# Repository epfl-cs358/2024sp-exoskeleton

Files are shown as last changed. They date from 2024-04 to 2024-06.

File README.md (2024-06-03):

# 2024sp-exoskeleton

<!-- PROJECT SHIELDS -->
<!--
-->
[][contributors-url]
[][license-url]

### Authors
- [Ewa Miazga](https://github.com/ewaMiazga)
- [Gabin Forestier](https://github.com/ForestDope)
- [Wei-En Hsieh](https://github.com/annhit29)
- [William Robert](https://github.com/AgeX21)
- [Benoit Morawiec](https://github.com/markh0rr)
- [Haris Malik](https://github.com/harismalik-1)

<!-- MARKDOWN LINKS & IMAGES -->
<!-- https://www.markdownguide.org/basic-syntax/#reference-style-links -->
<!-- change the contributors page -->

<!-- TABLE OF CONTENTS -->
<details>
  <summary>Table of Contents</summary>
  <ol>
    <li>
      <a href="#about-the-project">About The Project</a>
      <ul>
        <li><a href="#built-with">Built With</a></li>
        <li><a href="#motivation">Motivation</a></li>
        <li><a href="#goal">Goal</a></li>
        <li><a href="#final-result">Final Result</a></li>
      </ul>
    </li>
    <li>
      <a href="#getting-started">Getting Started</a>
      <ul>
        <li><a href="#prerequisites">Prerequisites</a></li>
      </ul>
    </li>
    <li>
      <a href="#building-the-exoskeleton">Building the Exoskeleton</a>
      <ul>
        <li><a href="#mechanical-parts">Mechanical Parts</a></li>
        <li><a href="#assembly">Assembly</a></li>
        <li><a href="#electronics">Electronics</a></li>
      </ul>
    </li>
    <li><a href="#software">Software</a></li>
    <li><a href="#problems">Problems</a></li>
    <li><a href="#possible-improvements--extensions">Possible Improvements & Extensions</a></li>
    <li><a href="#license">License</a></li>
  </ol>
</details>

<!-- ABOUT THE PROJECT -->
## About The Project

<!-- MOTIVATION -->
### Motivation

Nowadays, hand exoskeletons are commonly used for rehabilitation therapy following health accidents such as strokes. Its efficacy in muscle memory training has the potential to be exploited in the fields of music, technology, and rehabilitation therapy.

Our project aims to facilitate muscle memory training of various piano techniques for pianists seeking to strengthen specific muscles and refine pianistic skills with greater efficiency. By using a lightweight hand exoskeleton, we can enforce specific positions at a given rhythm that allows the user to acquire a specific technique more quickly compared to traditional training.

We want the user to be able to input a technique and a specific tempo that they wish to train using an accompanying software tied to the exoskeleton. This then allows the exoskeleton to reproduce the movements of the technique.

<p align="right">(<a href="#readme-top">back to top</a>)</p>

<!-- FINAL RESULT -->
### Final Result
At the end of the semester, we have an exoskeleton of a hand that functions as follows:

<p align="center">
    Demo GIF
</p>

See the demo of our project here: [Demo](./photos/demo.mp4)

Some photos for reference:

<p align="center">
     
     
</p>

It is controlled via a web application, which includes a feature for playing songs with preloaded files. Additionally, the device can record played pieces, aiding the learning process by allowing users to repeat the segments they prefer.
Each finger is operated by a separate motor, enabling simultaneous movement of all fingers. This design grants the device flexibility, allowing it to play almost any song desired.

<p align="right">(<a href="#readme-top">back to top</a>)</p>

<!-- GETTING STARTED -->
## Getting Started

<p align="right">(<a href="#readme-top">back to top</a>)</p>

<!-- BUILT WITH -->
### Built With 
* [][React-url]
* [][Python-url]
* [][Cpp-url]
* [][Flask-url]

<p align="right">(<a href="#readme-top">back to top</a>)</p>

<!-- PREREQUISITES -->
### Prerequisites

Comprehensive list of elements we used in our project along with needed equipment. To construct the device, one should
- buy:
  -	Arduino Uno Board
  -	Proto Shield ARDUINO V.R3
  -	Power supply GST60A12-P1J
  -	Board LM2596
  -	DC Power Jack PJ-102B
  -	4 Bowden cables
  -	4 Servo motors DMS15-270
  -	MIDI keyboard
  -	Velcro tape
  -	Sewing kit
  -	Threads
  -	Screws
  -	Small elastic bands

- have access to:
  -	3D printer with TPU filament
  -	3D printer with PET filament
  -	Laser cutting machine
  -	Plastic board 3mm
  -	MDF board 3mm
  -	Driller
  -	Bunch of different screwdrivers
  -	Soldering kit

<p align="right">(<a href="#readme-top">back to top</a>)</p>

<!-- BUILDING THE EXOSKELETON -->
## Building the Exoskeleton

<p align="right">(<a href="#readme-top">back to top</a>)</p>

<!-- MECHANICS -->
### Mechanics Parts
The comprehensive list of all the elements to start:
- [x] 4 adjustable finger wraps
- [x] 4 finger Bowden end place holders
- [x] 4 Bowden cable guide fingers
- [x] 1 Bowden cables guide hand
- [x] 1 Bowden cables guide wrist
- [x] 1 forearm top holder
- [x] 1 motor mounting plate
- [x] 1 forearm top holder with cables passthrough
- [x] 1 Arduino and power supply bottom plate
- [x] 4 forearm attachments
- [x] 4 Bowden cable motor attachments
- [x] 4 Bowden inside board holders
- [x] 2 logo sides

To construct the device, one should first print all the necessary elements using 3D printers:

* For 3D printer with PET filament: [STL files](stl_files/pet_3d_print)  
* For 3D printer with TPU filament: [STL files](stl_files/tpu_3d_print)  

Then all the necessary elements need to be laser cut:

* On plastic 3mm board: [DXF files](dxf_files)

### Assembly

<p align="center">
    
</p>

Steps to put the device together:

1. Place threads into holes of Bowden cable guides (hand and wrist)

2. Glue Velcro straps to:
   - a. Bowden cable guides hand
   - b. Bowden cables guides wrist
   - c. 4 forearm attachments

<p align="center">
    threads_photo
</p>

3. To each of adjustable finger wraps, one should glue:
   - a. Finger Bowden end placeholders
   - b. Bowden cable guide fingers

<p align="center">
    
</p>

4. Screw motors to the motors mounting plate.

5. Screw logo sides to the motors mounting plate.

<p align="center">
    
</p>

6. Screw 2 forearm attachments to the forearm top holder which has the cables passthrough.

7. Screw 2 forearm attachments to Arduino and power supply bottom plate

<p align="center">
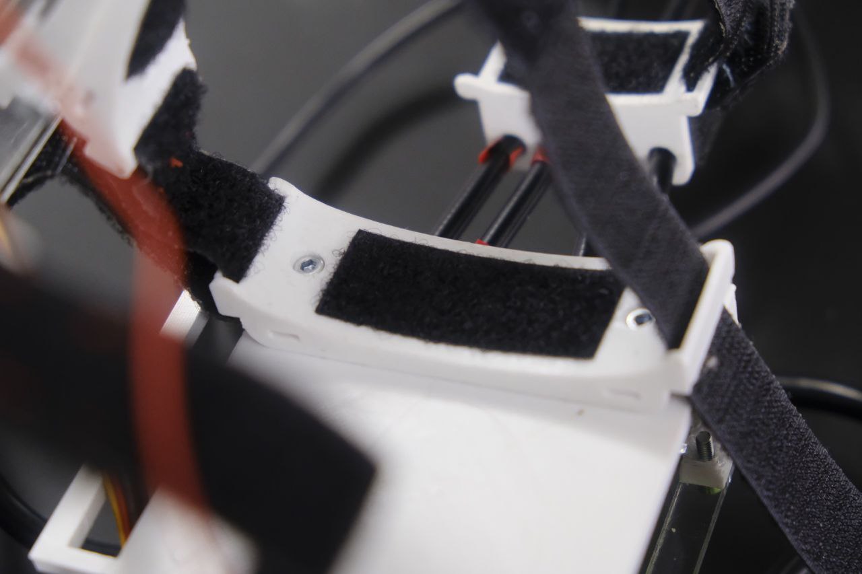
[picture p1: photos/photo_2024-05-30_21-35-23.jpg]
    
</p>

8. Solder all the necessary cables according to the scheme [Figure 2](#figure-2). For more details about soldering, go to section [Electronics](#electronics).

<p align="center">
     
     
</p>

9. Screw the Arduino board with Proto Shield and all soldered components to Arduino and power supply bottom plate.

10. Pass Bowden cables through:
    - a. Bowden cable guides hand
    - b. Bowden cables guides wrist
    - c. Forearm top holder

11. Adjust the length of the Bowden cables in a way that they fit the placement of the motors.

12. Secure the Bowden cables by placing screws in threads of:
    - a. Bowden cable guides hand
    - b. Bowden cables guides wrist

13. Solder a bulb at the end of each of the Bowden cables.

<p align="center">
    
</p>

14. Enclose the soldered bulb in the Bowden cable motor attachments using a screw.

<p align="center">
    
</p>

15. Glue all of Bowden inside board holders in correct places on the forearm top holder

16. Connect Bowden cable motor attachments with Bowden inside board holders using elastic bands. Use the reef knot.

<p align="center">
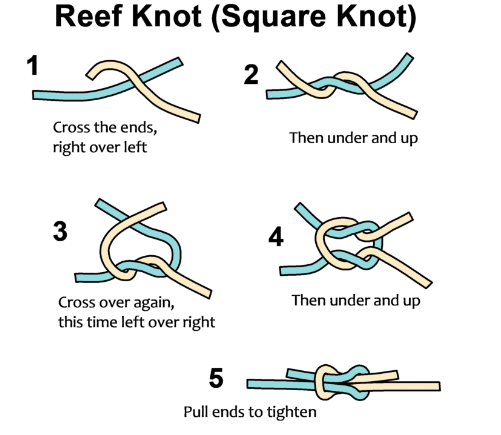
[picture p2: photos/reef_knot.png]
    
    
</p>

17. Attach Bowden cable motor attachments to the motors, so that they point towards the back (it enables half of the circle rotation to the front, and this push a finger down).

18. Screw the motors mounting plate to the forearm top holder.

<p align="center">
    
</p>

19. Sew Velcro straps to 
    - a. Bowden cable guides hand
    - b. Bowden cables guides wrist
    - c. 2 Bowden forearm attachments (on one of the sides of the Forearm top holder)

<p align="center">
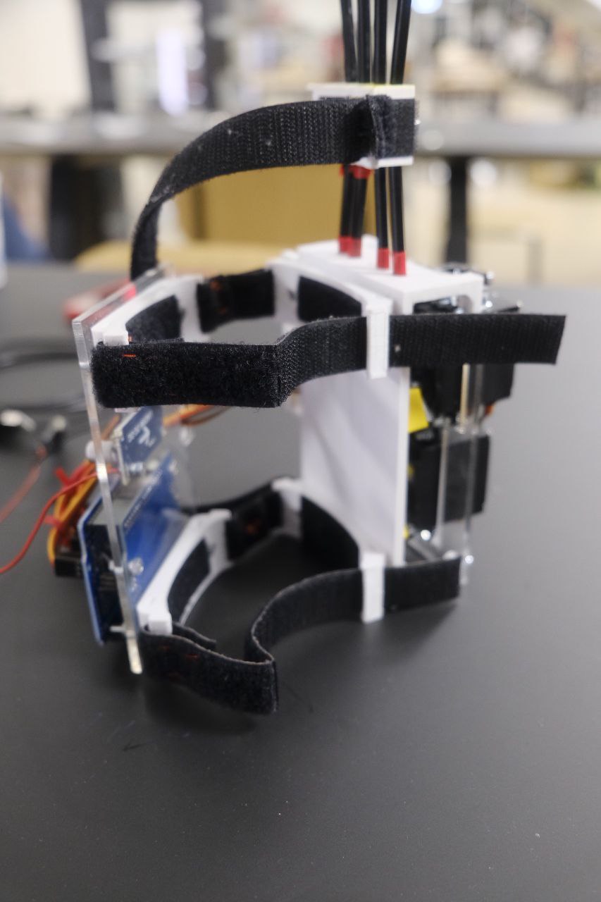
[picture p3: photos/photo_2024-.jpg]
    
</p>

20. Pass the motors’ cables through prepared space on 
    - a. Forearm top holder
    - b. Arduino and power supply bottom plate

<p align="center">
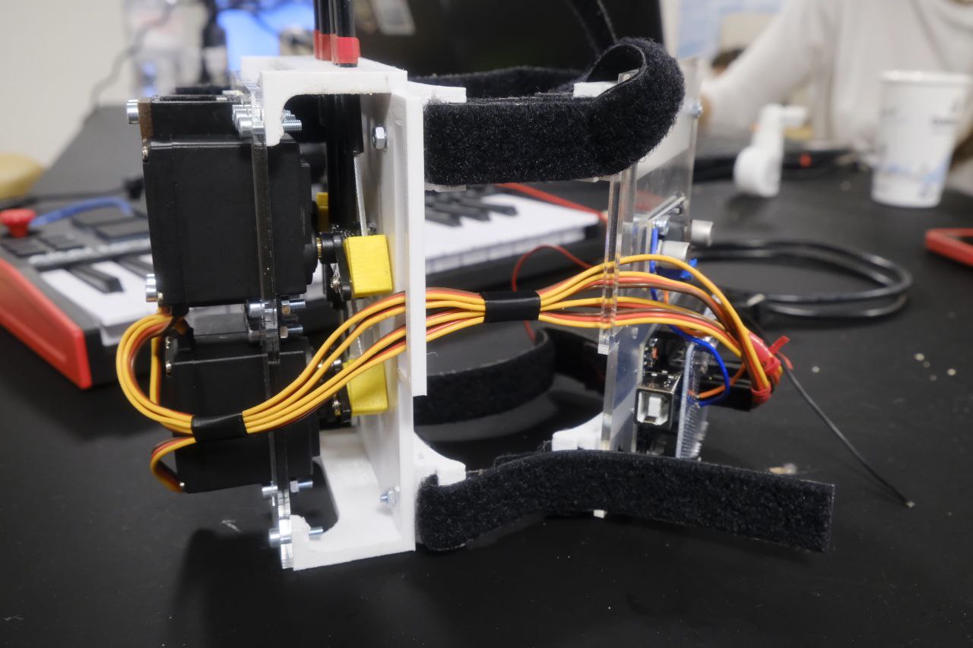
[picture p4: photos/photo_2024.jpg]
    
</p>

21. Attach the round end of the Bowden cable to the Bowden end place holders and force the cable into the finger guides.

22. Attach the logo at the top of the logo sides.

<p align="center">
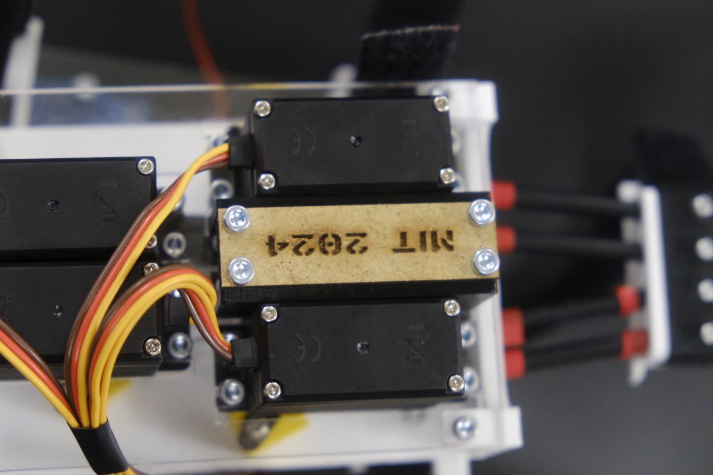
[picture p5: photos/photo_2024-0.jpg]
    
</p>

<p align="right">(<a href="#readme-top">back to top</a>)</p>

<!-- ELECTRONICS -->
### Electronics

For the electronics, we needed to power 4 6V servomotors so we couldn't use the Arduino 5V power supply. To solve this problem, we used a 12V power supply with a LM2596 voltage regulator to transform the 12V input into 6V. We then connected to 6V input to all the motors voltage input and did the same for the ground. The servomotors need a PWD arduino pin for control so we settle for the pin 3 5 9 and 11 because they don't touch each other so it would be simpler to solder everything. We also used an external arduino connection board to make everything look nicer.

You can see the schematics for the circuit here, the input is missing from the schematics but it goes on the left handside of the potentiometer : 

<p align="center">
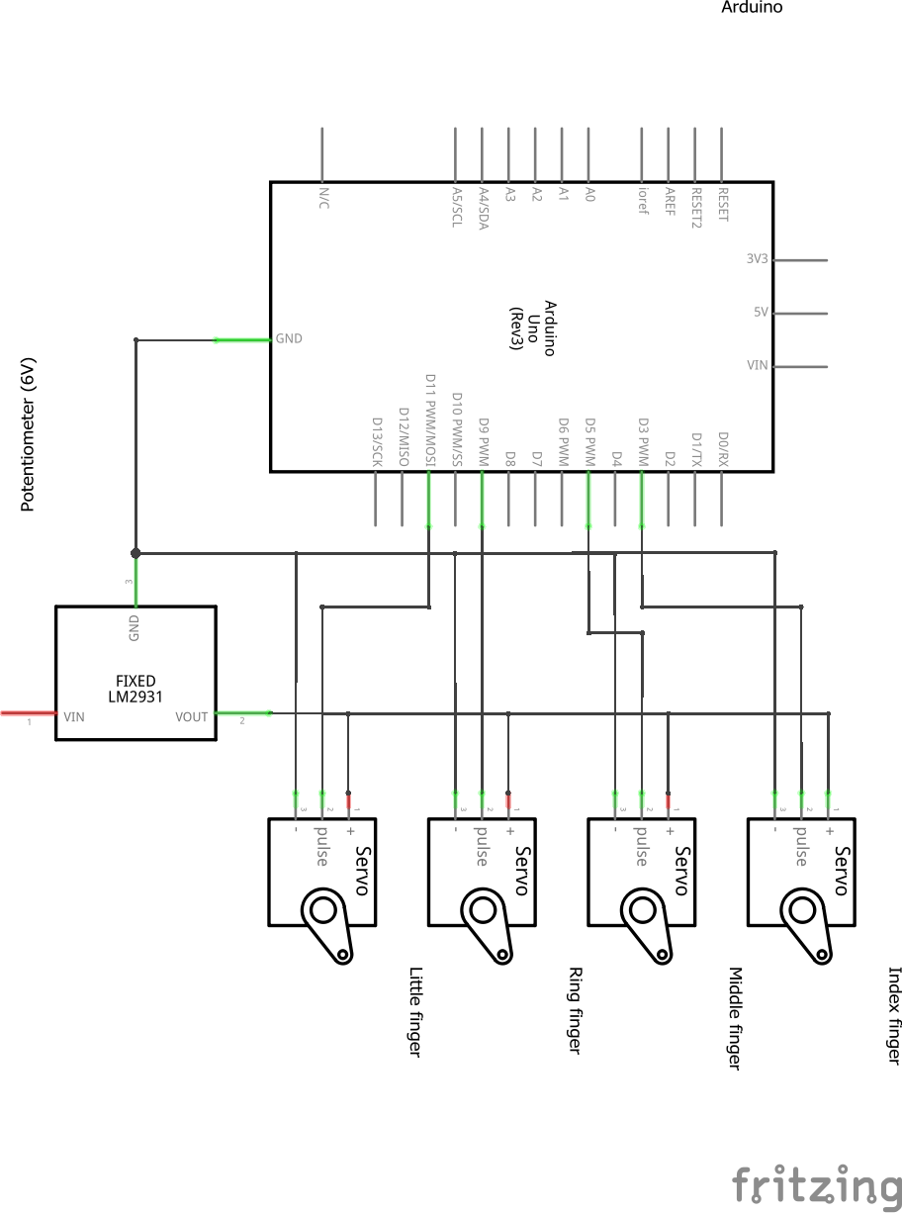
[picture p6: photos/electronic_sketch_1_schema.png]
    
</p>

*Figure 1: Schematic of the electronic sketch.*

Here is the same schematics but the added external board :

<p align="center">
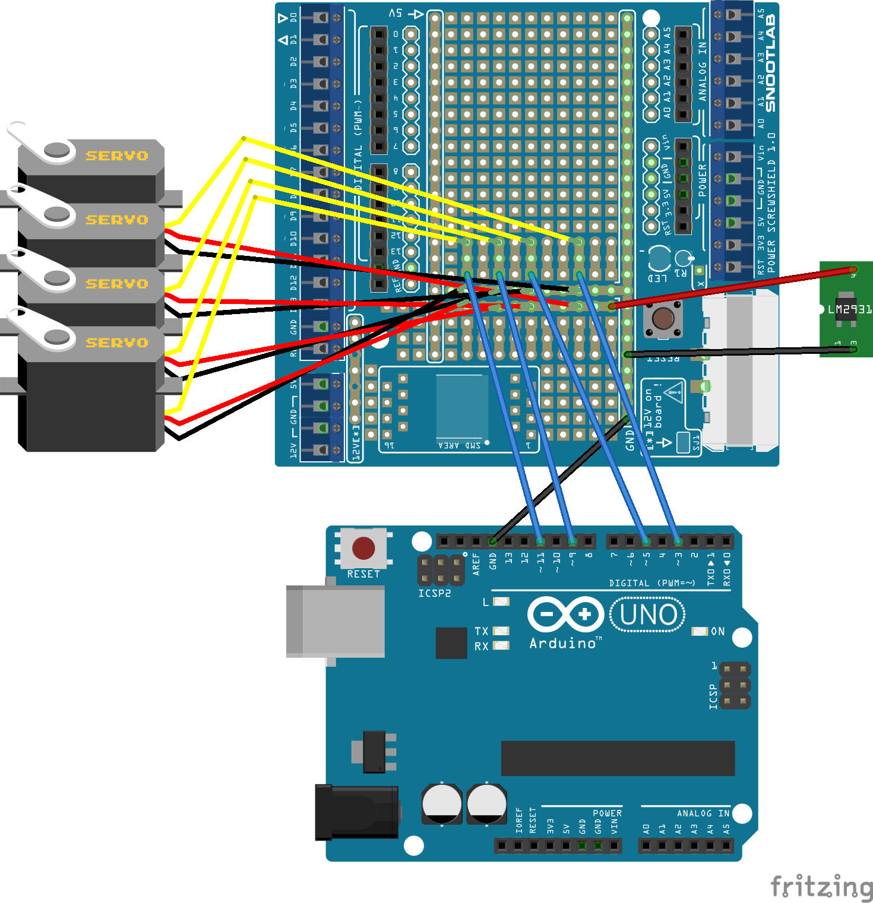
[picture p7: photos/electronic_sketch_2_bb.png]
    
</p>

*Figure 2: Schematic of the electronic sketch.*

Step by step guide to connect everything (using a breadboard):

1. solder the potentiometer LM2596 to the connector for the power supply and the other end to cables

2. connect the potentiometer out+ in one line in the breadboard, connect the out- to another line (must be different lines)

3. connect the ground of the arduino to the same line as the out-

4. Connect each motor to the breadboard as follows : red wire goes to out+, brown wire goes to out- and yellow wire is used for later

5. connect the yellow wire of each motor to the arduino on the pin 3 5 9 and 11, each pin correspond to a finger in increasing order (see schematics)

6. You're done !

<p align="right">(<a href="#readme-top">back to top</a>)</p>

<!-- SOFTWARE -->
## Software
We are building a Next.js App. 

We need to have two terminals to run the frontend (client end) and the backend (server end).

### Frontend
The frontend part is the client of the website, written in the TypeScript programming language.

#### Requirements
To run the frontend, please make sure you are in the `frontend` folder, please run the following command if not: 
```
cd .\frontend\
```
then 
```
npm install
```

If you have encountered the problem of `concurrently "npm run dev:next" "npm run dev:ws"`, please run:
```
npm install concurrently --save-dev
```

#### Run
```
npm run dev
```

#### Output
You will reach the welcome page
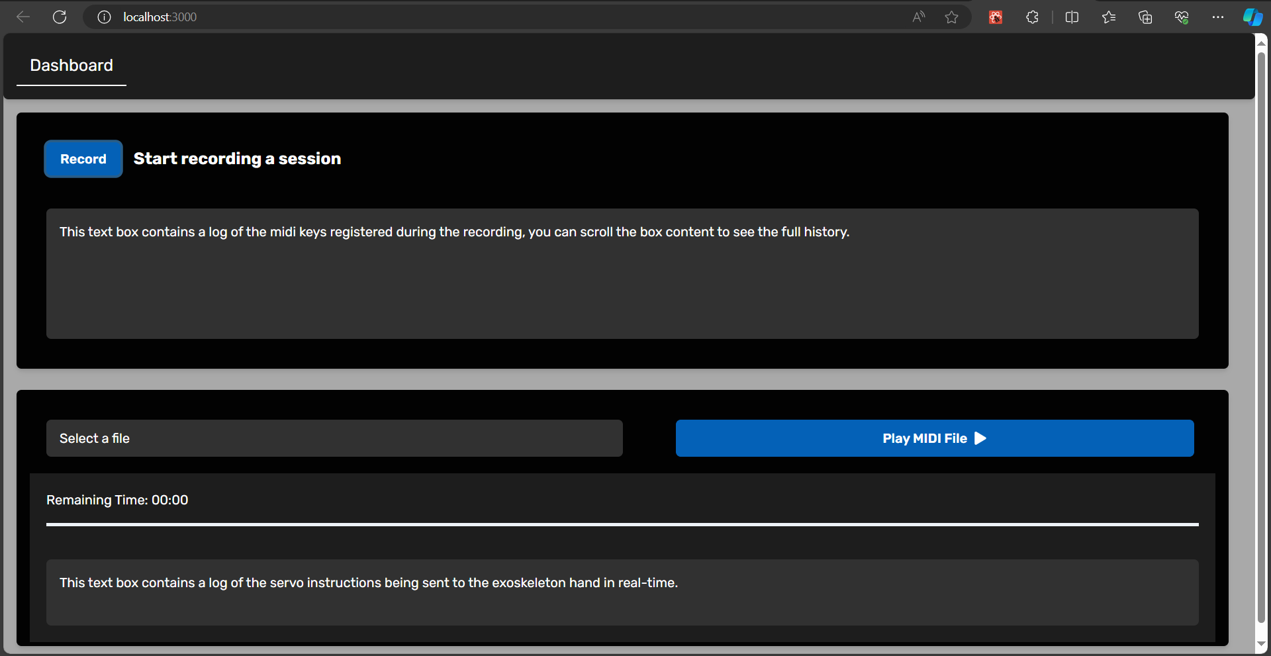
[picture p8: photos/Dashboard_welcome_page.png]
Dashboard welcome page


Now, we can record a piece after clicking on the "Record" blue button to record what we play, then stop recording by clicking on the "Recording ..." grey button, and then save the file.
We can also play songs, which are MIDI files, by clicking on "Play MIDI File" button after selecting a file with the "Select a file" button.

### Backend
The backend is made of a Flask server. It exposes the following functionalities to the WebApp: play a recording on the glove, start to record keypresses from the midi device and list existing recordings. The server listens for incoming HTTP requests. If the request corresponds to one of the two actions: play and record, the server schedules its execution by registering a new task intent in the job queue. A consumer thread periodically pulls the queue for new jobs. Below is the system architecture of the backend.

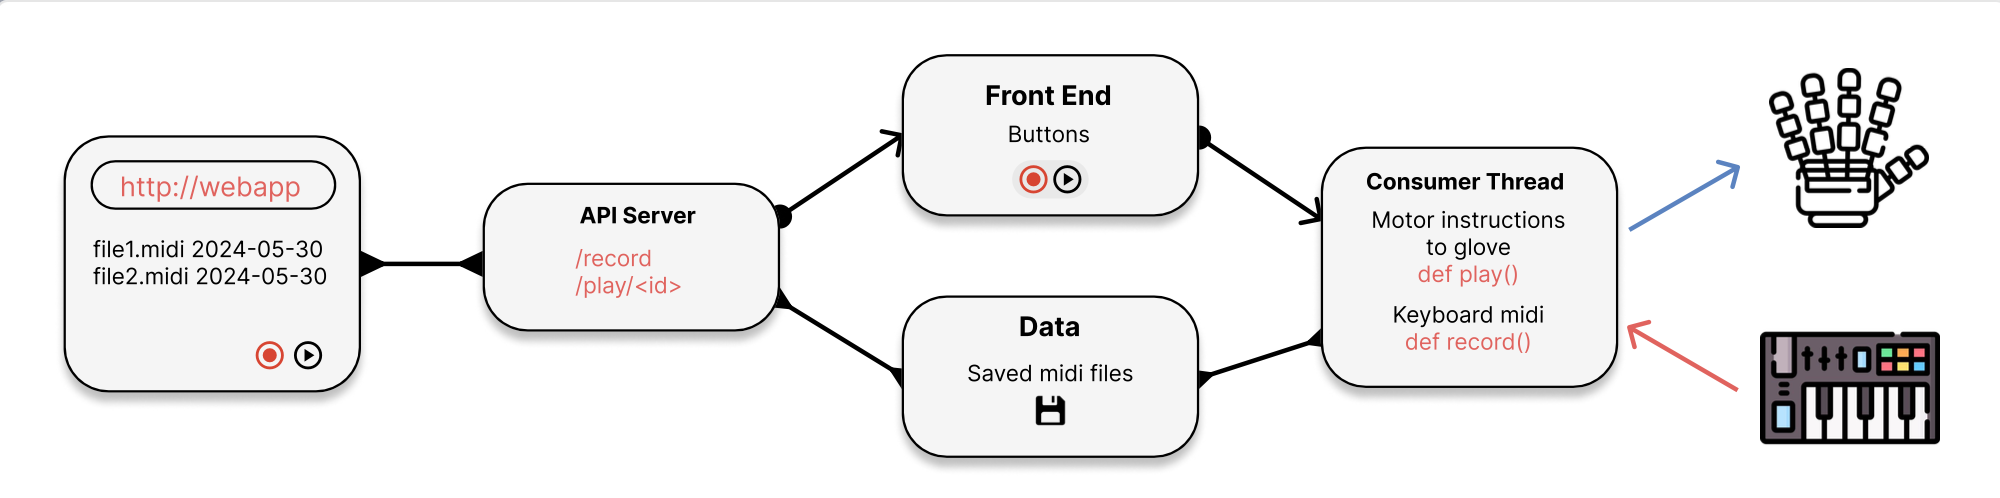
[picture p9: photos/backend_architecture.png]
backend architecture


#### Requirements

You will need python3 and pip3 to be installed on your system to run the backend.

The first step is to create a python virtual environment within `./backend`:
```
cd backend
python3 -m venv venv
```

Enable the virtual environment (Windows):
```
.\venv\Scripts\activate.bat
```

Enable the virtual environment (Mac and Linux):
```
source ./venv/bin/activate
```

Install the project dependencies:
```
pip3 install -r requirements.txt
```

#### Run

Make sure the Python virtual environment is enabled.

Then you can run the backend server with:
```
python3 ./src/main.py
```

### MIDI Interpreter

For the MIDI Interpreter, we used a python library called Mido to read and play the midifile live.
The MIDI Interpreter class has 6 main functions :

  1. __init__ : The starting point of the class, it opens the serial port and setup everything that has been given to it

  2. __write_read(x)__ : This is the function responsible for communicating with the arduino, both writing to the Serial port and reading from it.

  3. set_filename(x)__ : This function is used to switch midifile dynamically without restarting everything

  4. __preprocess()__ : This function looks through the midifile and make a list of playable note based on the amount of finger we want to play with, it takes the first note played as a base and uses a bound to reject note that a too far away from it (we can't play with one hand across 2 octaves). Once the file is over or if we have enough note to play, it returns.

  5. __interpret()__ : This function is the actual function responsible for playing the midifile, it takes the midifile currently opened in the class and the list of note to play and sends the appropriate message to the arduino to rotate the motor in the right direction.

  6. __play()__ : This function executes all sub-functions required to play a midifile.

<p align="right">(<a href="#readme-top">back to top</a>)</p>

## Problems
One of the main challenges in constructing the exoskeleton is determining the correct cable length. We experienced numerous iterations of cutting, soldering, and covering cables before achieving the proper lengths. Incorrect cable lengths prevent effective force transfer from the motors throughout the design, resulting in inadequate finger movement. It's crucial to adjust the cable length to fit the smallest potential user, as it can still be accommodated by larger users with closer placement on the hand.

Another significant issue is that the force is generated by pushing the cables rather than pulling them from the bottom. This makes the cables more susceptible to bending, which posed a considerable problem in our project. Although it may seem repetitive, the efforts to mitigate this issue are essential. The device is secured to the board with elastics that generate force towards the cable covers, and these measures are not redundant. The cables require multiple rigid components to prevent bending and ensure proper finger movement.

<p align="right">(<a href="#readme-top">back to top</a>)</p>

<!-- POSSIBLE IMPROVEMENTS & EXTENSIONS -->
## Possible Improvements & Extensions

### Hardware
Possible improvements for the hardware should include adding control for the thumb. This addition is more complex and requires a different approach compared to the finger attachments. 

To incorporate this feature, adjustments are needed in the initial design. Specifically, the wrist and palm stabilizing elements must be modified to accommodate a fifth cable, as there is currently no space for it. However, the motor fixation plate and electronics are already designed to support five motors, so no modifications are needed for these components.

### Software
The front-end web developer has developed the following screens:

Dashboard page:
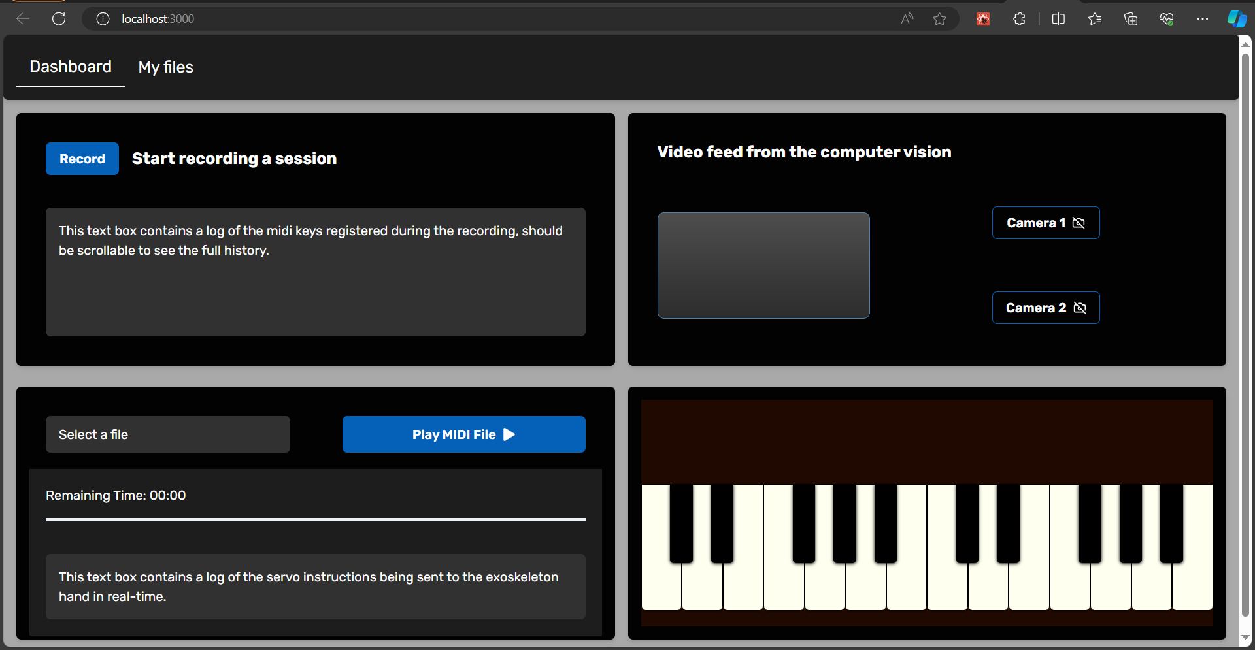
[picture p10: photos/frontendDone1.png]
frontendDone1


My_Files page:
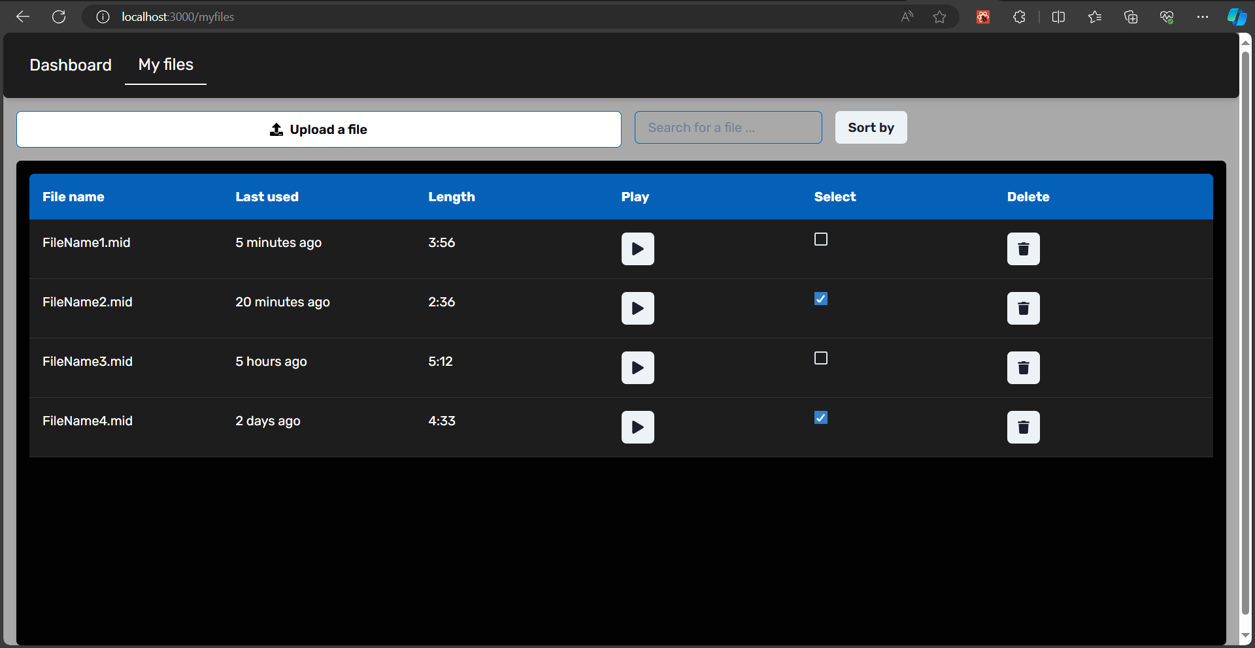
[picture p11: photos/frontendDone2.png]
frontendDone2


In the future, we will develop the Computer Vision part. So far, we have the fundamental part of Computer Vision which can track the hand.
There is also a piano visualizer that will be combined with the MIDI interpreter and the backend.

There is the My_Files page where the front-end and the back-end developers will combine the two ends. The current version of the My_Files page can see MIDI file information in detail such as the file name, the last used time, and the length. We can select and deselect MIDI files as well. In addition, we can search a file and sort the files. When the client (frontend) and the server (backend) communicate between themselves with websockets, we will be able to upload files from our computer, play and delete the existing MIDI files on the My_Files page.

<p align="right">(<a href="#readme-top">back to top</a>)</p>

## License

Distributed under the MIT License. See `LICENSE.txt` for more information.

<p align="right">(<a href="#readme-top">back to top</a>)</p>

<!-- MARKDOWN LINKS & IMAGES -->
<!-- https://www.markdownguide.org/basic-syntax/#reference-style-links -->
[contributors-shield]: https://img.shields.io/badge/CONTRIBUTORS-6-brightgreen?style=for-the-badge 
[contributors-url]: https://github.com/epfl-cs358/2024sp-exoskeleton/graphs/contributors
[license-shield]: https://img.shields.io/badge/LICENSE-MIT-brightyellow?style=for-the-badge
[license-url]: https://github.com/epfl-cs358/2024sp-exoskeleton/blob/main/LICENSE

[React.js]: https://img.shields.io/badge/React-black?logo=react
[React-url]: https://reactjs.org/
[Python.org]: https://img.shields.io/badge/Python-brightgreeen?style=flat&logo=python&logoColor=FFE873&color=306998
[Python-url]: https://www.python.org/
[Flask.com]: https://img.shields.io/badge/Flask-black?style=plastic&logo=flask&color=%2361dafb
[Flask-url]: https://flask.palletsprojects.com/en/3.0.x/
[Cpp.org]: https://img.shields.io/badge/C%2B%2B-blue?logo=cplusplus
[Cpp-url]: https://isocpp.org/

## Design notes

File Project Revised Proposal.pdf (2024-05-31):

## CS-358 Making Intelligent Things

## Revised Project Proposal, “Robotic Hand Exoskeleton for Enhancing Fingering Skills and Agility of Pianists”

Gabin Forestier, William Robert, Ewa Miazga, Wei-En Hsieh, Haris Malik , Benoît Morawiec

## Contents

## 1) Description and motivation

### Motivation

Nowadays, hand exoskeletons are commonly used for rehabilitation therapy following health accidents such as strokes. Its efficacy in muscle memory training has the potential to be exploited in the fields of music, technology, and rehabilitation therapy.

Our project aims to facilitate muscle memory training of various piano techniques for pianists seeking to strengthen specific muscles and refine pianistic skills with greater efficiency. By using a lightweight hand exoskeleton, we can enforce specific positions at a given rhythm that allows the user to acquire a specific technique more quickly compared to traditional training.

We want the user to be able to input a technique and a specific tempo that they wish to train using an accompanying software tied to the exoskeleton. This then allows the exoskeleton to reproduce the movements of the technique.

### How we achieve this

To let the user obtain pianistic skills with great efficiency, we build a hand exoskeleton that has both push and pull abilities onto the digits of the user. We also need to be able to gather data on the specific technique that needs to be reproduced in the exoskeleton, so that we can convert this information into mechanical instructions interpretable by the device. Finally, this needs to be nicely integrated into an interface (web for example) that facilitates the recording and replaying of sessions for the end user.

### The mechanical build

To create the hand exoskeleton, we use a combination of Bowden cables attached to nylon strings in order to pull the fingers inward of the palm and tension springs to pull them back.

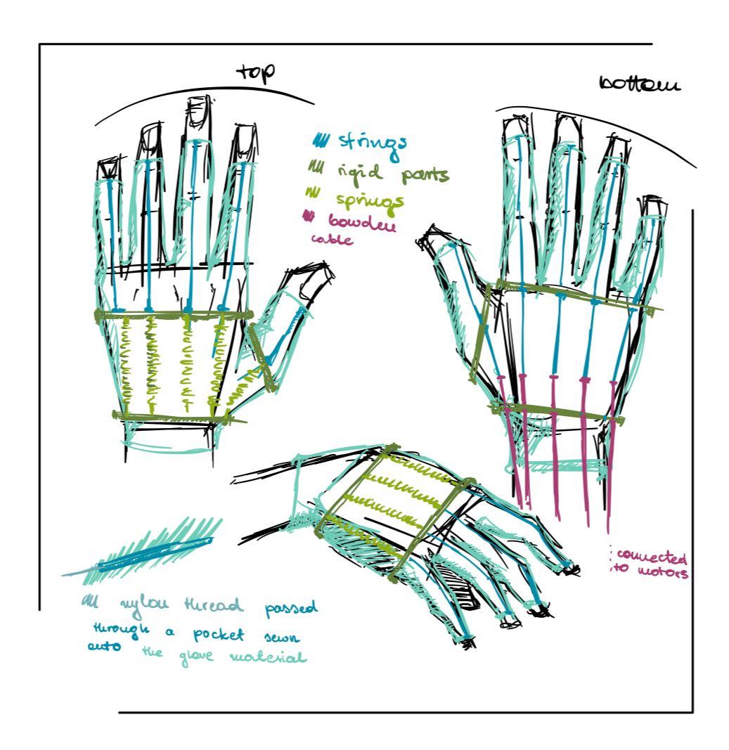
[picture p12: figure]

For the tensioning system, we use 5 servo motors, one per finger digit so that all motions are accurate. This involves designing 3D parts for the tensioning system such as spools to rotate the strings and create tension. All hand parts would be attached to an elastic fabric glove to fit a wider range of hand sizes and shapes.

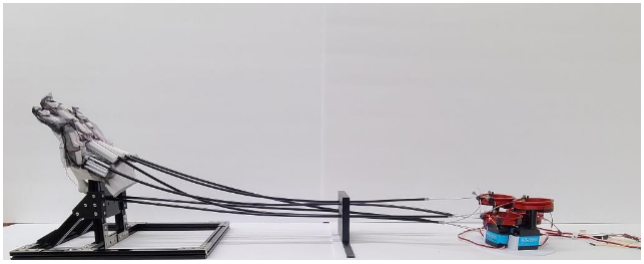
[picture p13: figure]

Project reference from Reference 1 (https://escholarship.org/content/qt5rz8n08x/qt5rz8n08x_noSplash_05dde0aa3c26d63ffef8eba12090ab96.pdf)

For safety and testing purposes, we would use a 3D-printed mannequin hand during the earlier stage of the project development. An existing model is available here. (https://grabcad.com/library/biomimetic-hand-v2-1)

### The software

### 1. Recording the data:

We first need to determine our source data which will be used to reproduce the technique played. Important factors include timing, force, and velocity. For this purpose, we have decided to use a MIDI keyboard as its MIDI interface allows us to gather information on when a key is pressed, how far it is pressed, and the velocity with which it is pressed, through MIDI messages that can be read over a USB connection to a computer.

Additionally, we can use computer vision with a smartphone camera to gather information on which finger pressed which key. In combination with the MIDI data, we should have enough information to reproduce the technique with a good degree of accuracy.

### 2. Interpreting the data:

Once we have acquired the data cited previously we need to process it through a coded interpreter, running on a computer, which will then output servo instructions to be executed using the Arduino UNO which connects the servo motors. This requires a careful analysis of the MIDI and computer vision data to obtain glove movement that mimics the recorded technique best.

Furthermore, we could also model our interpreter to translate only MIDI data (no computer vision) as many MIDI files are available online. This would allow users to train on a wider range of pieces which they are not familiar with. This would of course complexify the interpretation as we wouldn’t have information on which fingers are used. But this could be inferred with some clever logic and be serviceable.

### 3. Using the device:

Finally, we will design and code a web app interface, using html, in order to facilitate the use of the device. It would allow the user to easily launch a recording session, visualize the recorded data, process it, and then send the instructions to the device to start a training session.

## 2) Work breakdown

- (3D design in Fusion)
- (Hardware)
- (Software)

Week 7:

- Task 1: 3D print the mannequin hand to experiment without risking physical damage. ⧫
- Task 2: Design and print the servo motors’ enclosure and fixation plate in Fusion ⧫ ⧫
- Task 3: Start coding the software : retrieve the MIDI data coming from the keyboard. Store the data for later use. ⧫
- Task 4: Design and print the spools to be attached to the servo motors ⧫ ⧫

Week 8:

- Task 5: Design and print the 3D parts to attach the nylon strings to the fingers. ⧫ ⧫
- Task 6: Design and print the 3D part to hold the tension springs. ⧫ ⧫
- Task 7: Attach velcro patches to the dorsal part of the glove. ⧫
- Task 8: Design and print the Bowden cable holders. ⧫ ⧫
- Task 9: Start coding the interpreter for the MIDI data to servo motors instructions. ⧫
- Task 10: Design and print the hand holder. ⧫ ⧫

Week 9:

- Task 11: Cut the glove fingertips and attach 3D parts such as cables and spring holders. ⧫
- Task 12: Attach the nylon strings to the Bowden cables and the servo spools. ⧫
- Task 13: Assemble and connect the glove to the tensioning system, and fix it on the hand holder. ⧫
- Task 14: Continue the interpreter, and experiment with recording and replaying movements to fine-tune the translation of MIDI to servo motor instructions. ⧫

Milestone 1: The glove is fully assembled, movement is functional, and it can manually send commands to the servos to move the hand. The interpreter is partially coded. Estimated deadline: 28th April.

Week 10:

- Task 11: Finish the interpreter for the MIDI data to servo motors instruction. ⧫
- Task 12: Do end-to-end testing, record then replay, all using MIDI data, fine-tune and debug. ⧫ ⧫
- Task 13: Start coding the web app interface. ⧫
- Task 14: Fix any potential hardware-related problems. ⧫

Week 11:

- Task 15: Record video with a smartphone and transfer it to a PC in real time. ⧫
- Task 16: Start coding computer vision to detect individual finger presses. ⧫
- Task 17: Continue the web app interface, should be able to start recording and replaying directly from it, and also visualize MIDI data in real time. ⧫

Milestone 2: The web app interface allows registering key presses through MIDI and replaying them through the glove manually. Which fingers to press which keys are manually set. Estimated deadline: 12th May.

Week 12:

- Task 18: Continue computer vision development, should be able to precisely determine which fingers are pressing a key at a certain time. ⧫
- Task 19: The web app interface should be able to display the computer vision visualization in real time. ⧫
- Task 20: Start coding the combination of the MIDI data with the computer vision data to generate motor instructions for the right fingers automatically. ⧫

Week 13 :

- Task 19: Finish the implementation of the computer vision data in the interpreter. ⧫
- Task 20: Fine-tune every aspect of the project if it is not already as intended. ⧫ ⧫

Milestone 3: The interpreter is linked with computer vision to automatically map keypresses to fingers, a video feed is also integrated into the web app interface. Estimated deadline: 26th May

Optional goals: The hand exoskeleton can replay without computer vision by inferring which finger is pressed. If for some reason we cannot get computer vision to nicely work we can drop it and base everything on the MIDI data. But it can also be a useful feature even if computer vision is working.

## 3) Bill of materials

# | Item name | Quantity (Price/item) | Redundancy

1 | Arduino Uno Board (in stock) | 1 (5.-) | 0
2 | Stretch Gloves size M (https://www.decathlon.ch/fr/p/sous-gants-en-soie-de-trekking-montagne-mt-500-noir-adulte/_/R-p-14734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) | 1 (14.90) | 1
3 | Bowden cables (https://www.reichelt.com/ch/en/bike-bowden-cable-universal-75-cm-bike-42300-p267135.html?trstct=pos_6&nbc=1) | 5 (1.67) | 5
4 | Tension springs (https://www.3dware.ch/en/accessories/mechanics-accessories/3dware-ch-handelsware-01900917-25-tension-spring-5-mm-36-5mm-25mm) | 5 (0.6) | 5
5 | Servo motors DMS15 (in stock) | 5 (5.-) | 2
6 | Nylon strings (https://www.fruugoschweiz.com/120m-nylon-anti-pull-cut-ly-wear-ant-bite-ant/p-275420695-611922938?language=fr) | 1 (7.-) | 0
7 | MIDI keyboard (https://www.thomannmusic.ch/intl/akai_mpk_mini_mk3.htm) | 1 (97.-) | 0
8 | Velcro tape (https://www.galaxus.ch/en/s4/product/delock-velcro-50-mm-velcro-tape-14338001) | 1 (6.45) | 0
9 | Sewing kit (https://www.manor.ch/de/p/mp-93820091-tproduct) | 1 (8.90) | 0

This table gives the number and price of each item we would need for the project and the number of spare parts we want to have some margin of error for testing and experimenting.

## 4) Risk Assessment

Risk 1: Thumb Movements

There's a risk that the device could restrict the freedom of movement of the fingers or not accurately translate the intended motions, especially that of the thumb.

Solution: Adapt the springs with a given hand dimension to have a natural feeling of playing the piano.

Risk 2: Computer Vision

Implementing computer vision to accurately track finger movements and key presses on a piano in real time could be challenging due to varying lighting conditions and the speed of finger movements.

Solution: Drop computer vision and instead, design a clever algorithm to infer finger positions based on the MIDI data. The timing and ID of the key pressed can be used to deduce which fingers are used.

Risk 3: Springs are not suited

It is possible that when assembling the hand exoskeleton it turns out that springs are not adequate to pull back the fingers as they could feel unnatural and uncomfortable to the user.

Solution: We could make the nylon strings wrap around the hand so they are connected to other Bowden cables on the dorsal side of the glove, we can then adapt the tensioning system to be able to pull in opposite directions.

## 5) Bibliography

1) Wearable Assistive Hand Exoskeleton for Activities of Daily Living (https://escholarship.org/content/qt5rz8n08x/qt5rz8n08x_noSplash_05dde0aa3c26d63ffef8eba12090ab96.pdf)
2) DextrEMS: Increasing Dexterity in Electrical Muscle Stimulation by Combining it with Brakes (https://github.com/humancomputerintegration/dextrEMS)
3) Fully Wearable Actuated Hand Exoskeleton for Assistance in Daily Life and Therapy (https://www.research-collection.ethz.ch/bitstream/handle/20.500.11850/358101/Thesis_TB_NoCV_Upload-compressed.pdf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)
4) Hybrid-Exoskeleton-Glove (https://github.com/newdexterity/Hybrid-Exoskeleton-Glove?tab=readme-ov-file)
5) Hand Exoskeleton for Rehabilitation (https://sist.sathyabama.ac.in/sist_naac/documents/1.3.4/b.e-ece-batchno-182.pdf)

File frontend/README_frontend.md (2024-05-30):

0) Requirements

```
npm install 
```

1) After running the web by entering the command `npm run dev` in the terminal, we see the following message:

```
> cs358-web-app@0.1.0 dev
> concurrently "npm run dev:next" "npm run dev:ws"

[0]
[0] > cs358-web-app@0.1.0 dev:next
[0] > next dev
[0]
[1]
[1] > cs358-web-app@0.1.0 dev:ws
[1] > node --loader ts-node/esm src/server.mts
[1]
[1] (node:29956) ExperimentalWarning: `--experimental-loader` may be removed in the future; instead use `register()`:
[1] --import 'data:text/javascript,import { register } from "node:module"; import { pathToFileURL } from "node:url"; register("ts-node/esm", pathToFileURL("./"));'
[1] (Use `node --trace-warnings ...` to show where the warning was created)
[0]   ▲ Next.js 14.2.3
[0]   - Local:        http://localhost:3000
[0]
[0]  ✓ Starting...
[0]  ✓ Ready in 3s
```

I am using
```
"dev:ws": "node --loader ts-node/esm src/server.mts",
```
in the `scripts` for this project. 
You can find it out in `package.json` file.

\
As I use `mts` file for the `server.mts` file, I configured the project with the `--loader` feature.

The use of `--loader` option gives us the following warning:
```
[1] > node --loader ts-node/esm src/server.mts
[1]
[1] (node:29956) ExperimentalWarning: `--experimental-loader` may be removed in the future; instead use `register()`:
[1] --import 'data:text/javascript,import { register } from "node:module"; import { pathToFileURL } from "node:url"; register("ts-node/esm", pathToFileURL("./"));'
[1] (Use `node --trace-warnings ...` to show where the warning was created)
```
Do not be scared by this. It does not affect the project. This warning is an `ExperimentalWarning`: it is telling us the `--loader` option is still experimental in Node.js. It is not yet stable and may change or be removed in future versions of Node.js. This means: as long as my **current** setup works correctly and I am aware of the experimental nature of the feature, ths use of `--loader` option does not break this project. It is very unlikely to have furthur updates and changes about this experimental loader feature. **Do not worry, I will follow Node.js updates to stay informed about the status of the `--loader` experimental feature.**

2) To run the client end and the server end with only one command `npm run dev` (which is extremely useful haha), I configured the `scripts` of the project to run concurrently two commands:
```
    "dev": "concurrently \"npm run dev:next\" \"npm run dev:ws\"",
```
Please refer again to the file `package.json`.

\
Sidenote: Although the configuration of the websockets for the web has taken me time and many efforts (to search online and ask many questions to AI tools, *which is, I assume, very normal in Computer Science in general*), so to make everything compatible in this project, in order to have the websockets that work, I still need to say I love the lovely Computer Networks 💓💓

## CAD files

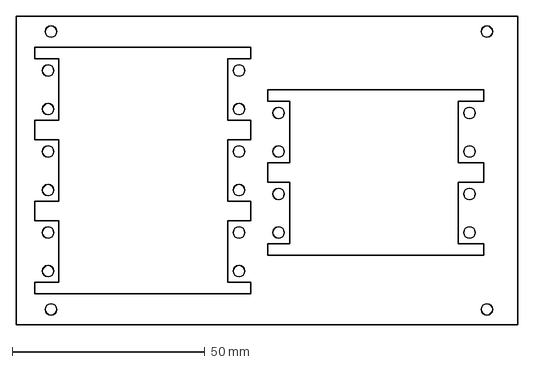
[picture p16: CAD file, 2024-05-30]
dxf_files/motor_mouting_plate.dxf
130.0 x 80.0 mm

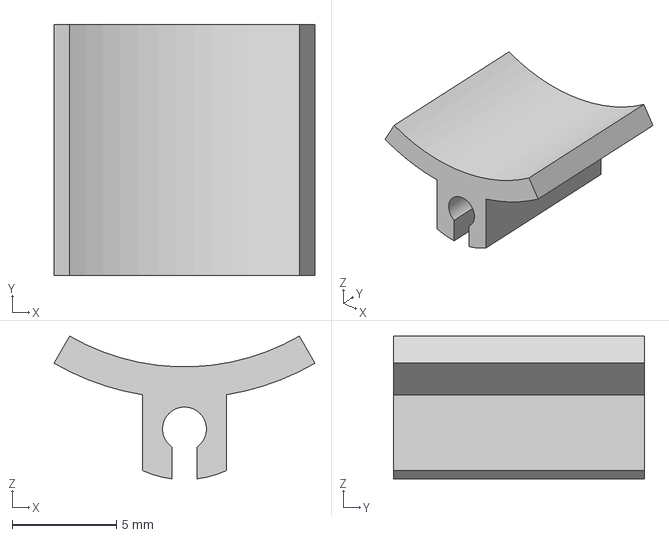
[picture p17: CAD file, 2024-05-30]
step_files/bowden_cable_guide_finger.step
12.5 x 12.0 x 6.84 mm

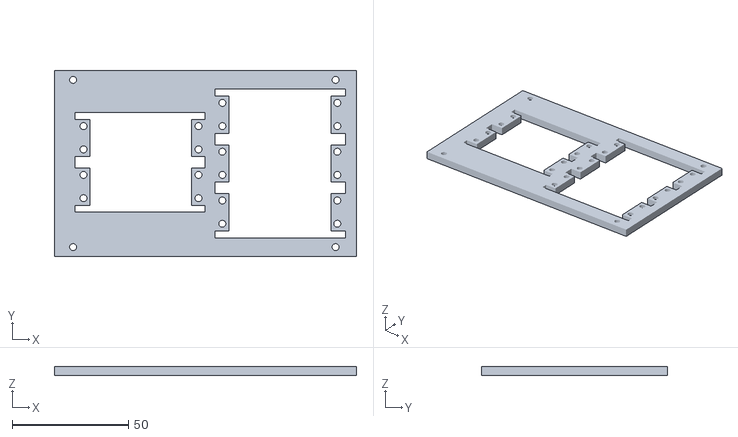
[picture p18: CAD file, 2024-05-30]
stl_files/motors_mounting_plate.stl
130.0 x 80.0 x 4.00

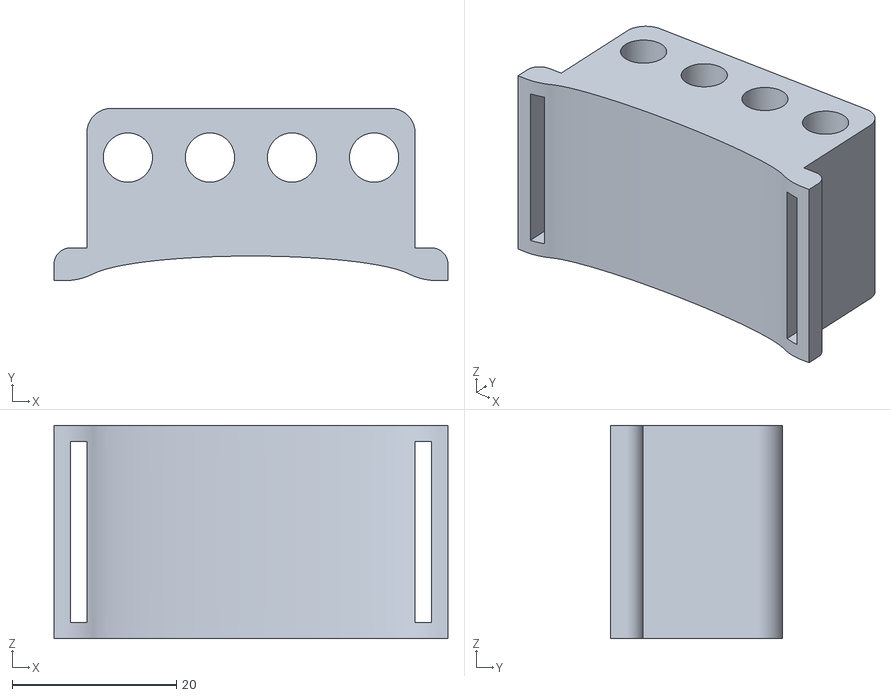
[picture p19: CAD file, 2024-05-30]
stl_files/pet_3d_print/bowden_cable_guides_wrist.stl
48.0 x 21.0 x 26.0

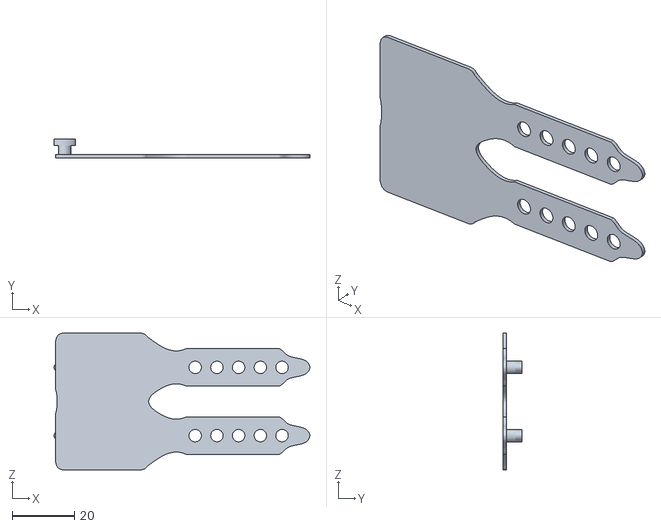
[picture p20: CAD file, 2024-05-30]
stl_files/tpu_3d_print/adjustable_finger_wraps.stl
82.5 x 6.00 x 44.0

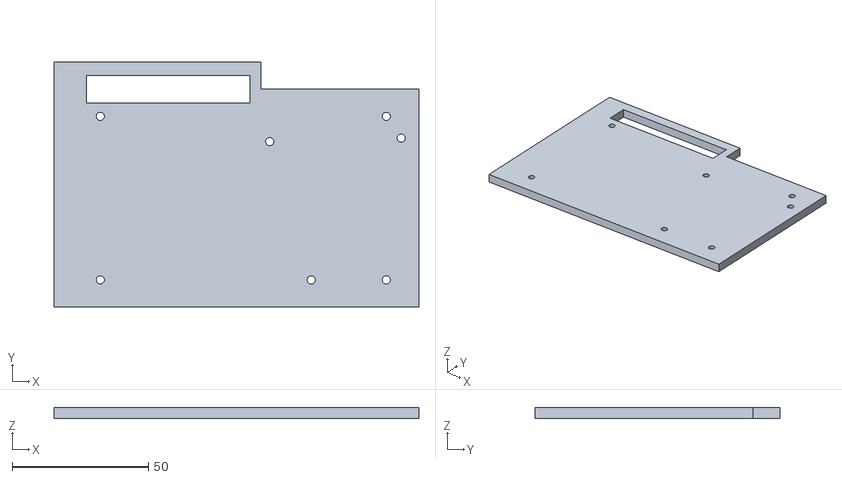
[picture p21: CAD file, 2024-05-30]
stl_files/arduino_and_power_supply_bottom_plate.stl
134.0 x 90.0 x 4.00

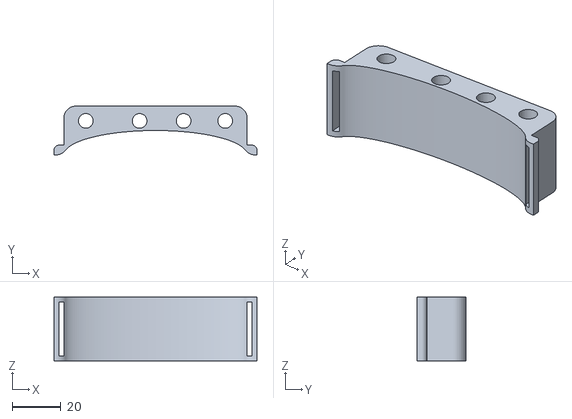
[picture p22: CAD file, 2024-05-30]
stl_files/pet_3d_print/bowden_cable_guides_hand.stl
83.0 x 20.0 x 26.0

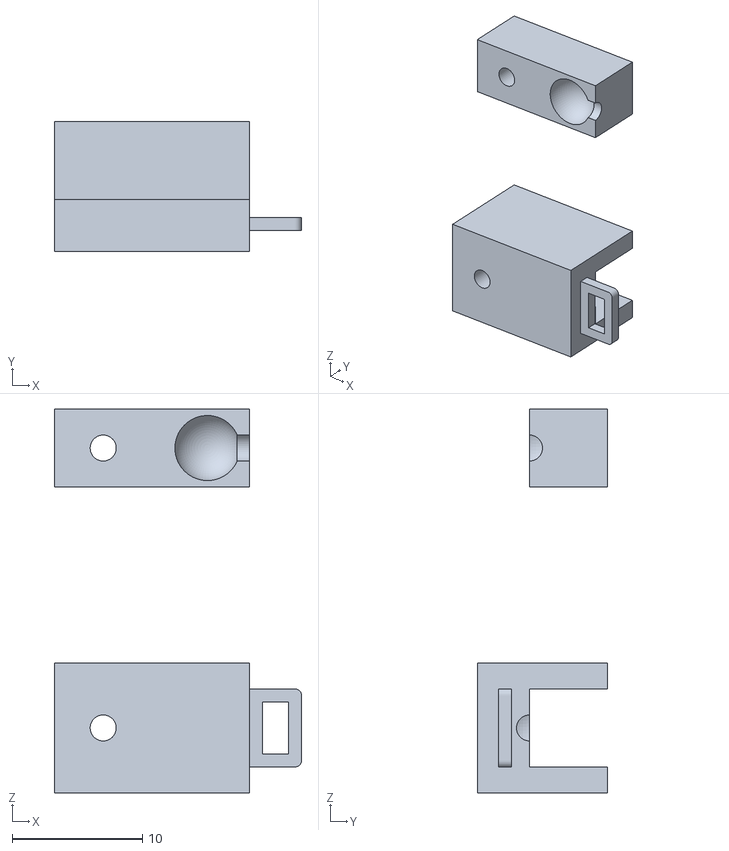
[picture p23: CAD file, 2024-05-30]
stl_files/pet_3d_print/bowden_cable_motor_attachment.stl
19.0 x 10.0 x 29.5

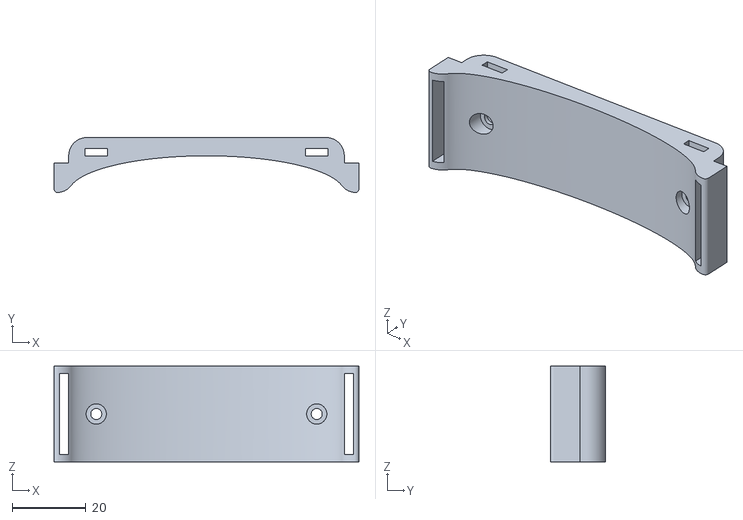
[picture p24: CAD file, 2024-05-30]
stl_files/pet_3d_print/forearm_attachment.stl
83.0 x 15.0 x 26.0

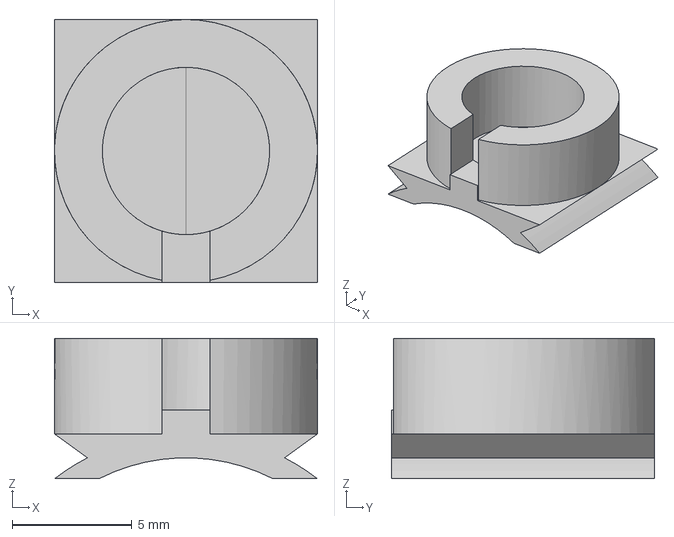
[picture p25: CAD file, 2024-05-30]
step_files/finger_bowden_place_holder.step
11.0 x 11.0 x 5.88 mm

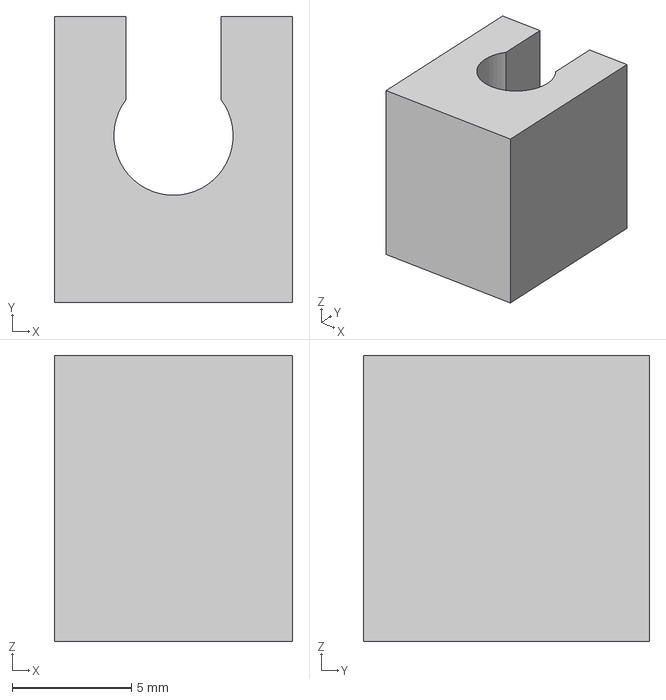
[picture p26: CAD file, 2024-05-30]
step_files/bowden_inside_board_holder.step
10.0 x 12.0 x 12.0 mm

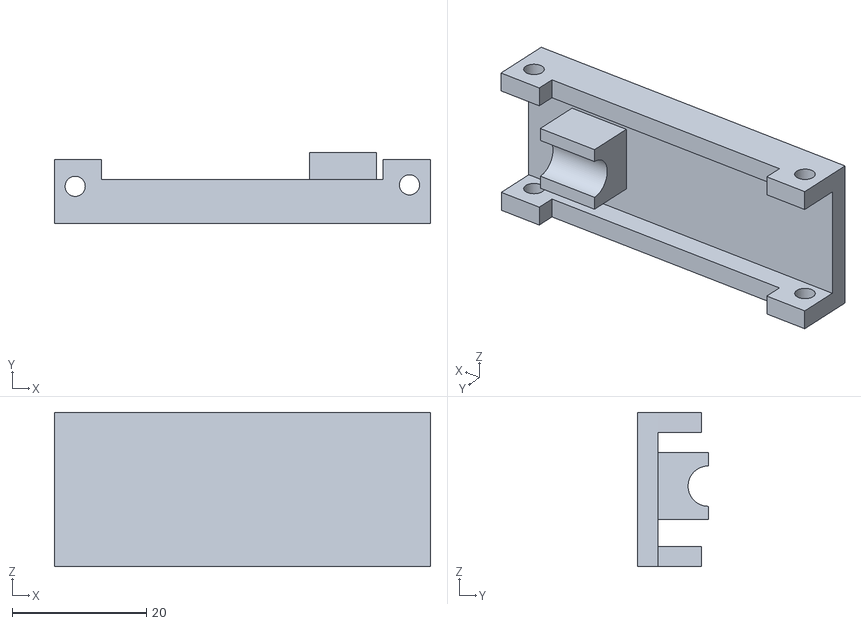
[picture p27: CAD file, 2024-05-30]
stl_files/pet_3d_print/logo_holder_sides.stl
56.0 x 10.5 x 23.0

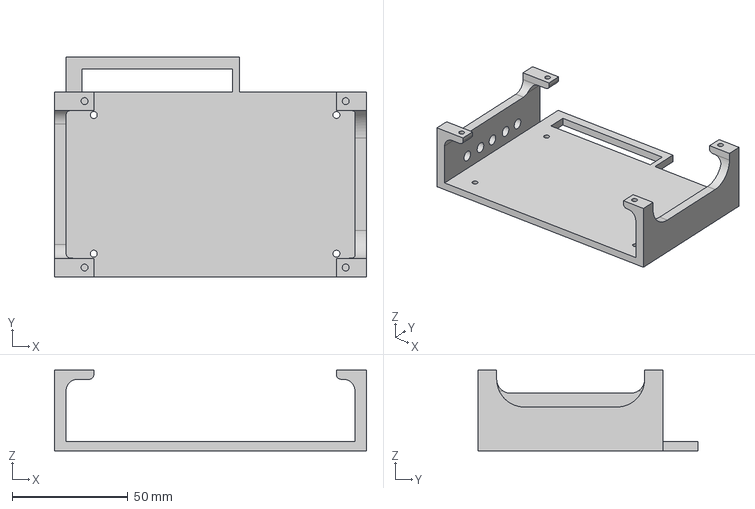
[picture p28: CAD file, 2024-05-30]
step_files/motor_holder_parts.step
135.0 x 95.0 x 35.0 mm

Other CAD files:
step_files/adjustable_finger_wrap.step
step_files/bowden_cables_guides_wrist.step
step_files/bowden_cable_motor_attachment.step
stl_files/pet_3d_print/finger_bowden_end_place holder.stl
stl_files/pet_3d_print/bowden_cable_guide_fingers.stl
dxf_files/arduino_and_power_supply_bottom_plate.dxf
f3d_files/adjustable_finger_wrap.f3d
f3d_files/arduino_and_power_supply_bottom_plate.f3d
f3d_files/bowden_cable_guide_finger.f3d
f3d_files/bowden_cable_motor_attachment.f3d
f3d_files/bowden_cables_guides_wrist.f3d
f3d_files/bowden_inside_board_holder.f3d
f3d_files/finger_bowden_place_holder.f3d
f3d_files/forearm_attachment.f3z
f3d_files/logo_sides.f3d
step_files/forearm_attachment.step
step_files/logo_sides.step
stl_files/pet_3d_print/bowden_inside_board_holder.stl
stl_files/pet_3d_print/forearm_top_holder_with_cables_passthrough.stl

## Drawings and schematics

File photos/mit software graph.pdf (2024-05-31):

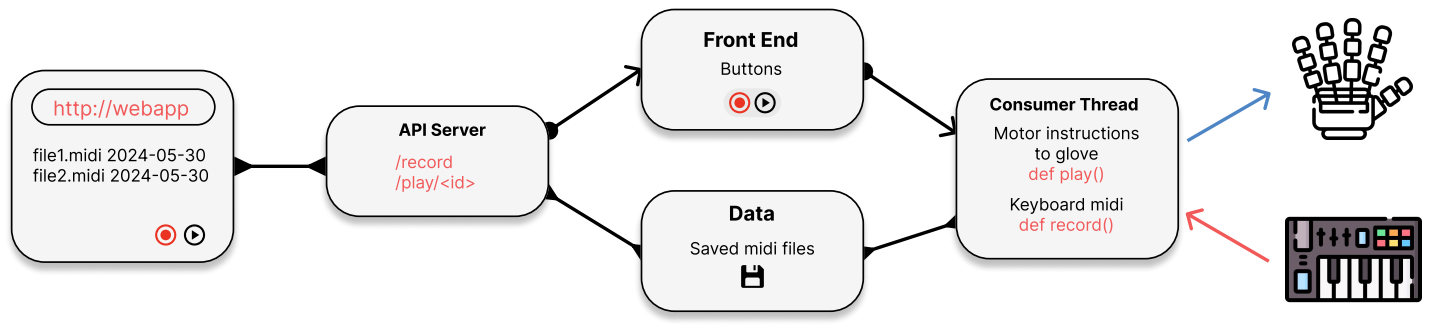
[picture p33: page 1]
http://webapp; file1.midi 2024-05-30; file2.midi 2024-05-30; API Server; /record /play/<id>; Data; Front End; Buttons; Keyboard midi; def record(); Motor instructions; to glove def play(); Consumer Thread

Saved midi files

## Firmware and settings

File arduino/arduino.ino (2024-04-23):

#include "Servo.h"

int motors[5] = {0, 0, 0, 0, 0};
int delay_motors[5] = {-1, -1, -1, -1, -1};
Servo servo[5];
const byte servoPins[] = {3,5,6,9,10};

void setup() { 
	Serial.begin(115200);
  Serial.setTimeout(0.1);
  for(int i = 0; i < 5; i++)
  {
    servo[i].attach(servoPins[i]);
  }
} 


void loop() {
  processInput();
  for(int i = 0; i < 5; i++)
  {
    if(delay_motors[i] != -1 && delay_motors[i] < millis()) stop_motor(i);
  }
}


void processInput() {
  if(Serial.available() > 0){
    delay(5);
    String input = Serial.readStringUntil("\n");
    input.trim();

    if (input.startsWith("m")) {
    // Remove the "m" tag from the input string
    input.remove(0, 1); // Remove the first character (tag)
    input.trim();

    int motor, speed, delay;
    // Parse the three integers separated by spaces
    int parsedCount = sscanf(input.c_str(), "%d %d %d", &motor, &speed, &delay);

    if (parsedCount == 3) {
      // Successfully parsed three integers
      motor_control(motor, speed, delay);
    } else {
      Serial.println("Failed to parse integers, here is the string : " + input);
    }
  }
  }
}

void motor_control(int motor, int speed, int delay)
{
  if(speed < 1500)
  {
    if(motors[motor] == 1)
    {
      motors[motor] = 0; 
    }
    else return;
  }
  else {
    if(motors[motor] == 0)
    {
      motors[motor] = 1; 
    }
    else return;
  }

  Serial.println("Rotating Servo " + String(motor) + " with speed " + String(speed-1500) + " for " + String(delay) + " milliseconds.");
  servo[motor].writeMicroseconds(speed);
  delay_motors[motor] = millis() + delay;
}

void stop_motor(int motor)
{
  Serial.println("Stopping Servo " + String(motor));

  servo[motor].writeMicroseconds(1500);
  delay_motors[motor] = -1;
}

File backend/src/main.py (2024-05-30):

import shared_data
import api
import core

if __name__ == "__main__":
    core.consummer_thread.start()       ## start the consummer thread 
    api.app.run(port=8080)  ## start the webserver
    print("[+] web app finished")
    shared_data.setProgramFinished()    
    core.consummer_thread.join()
    print("[+] thread finished")

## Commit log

2024-04-17 Part one and two of "Start coding the interpreter for the MIDI data to servo motors instructions."
2024-04-19 basic interpretation of the command, need others part to test further. Still have problem getting the data from python
    [arduino.ino]
2024-04-19 fixed the problem, forgot to reset motors in motor_up
    [midi_interpreter2.py]
2024-04-19 pushed the wrong file, this is the fix
    [arduino.ino]
2024-05-15 ServoMotorInstruction screen implemented
2024-05-20 tab switch in topbar works correctly
2024-05-20 new midi_interpreter for position servos
2024-05-21 modal for selecting a file in Dashboard's ServoMotorInstruction interaction OK
2024-05-21 new motor script
2024-05-21 ServoMotorInstruction and RemainingTime components' Play Pause button work correctly
2024-05-21 ServoMotorInstruction and RemainingTime components' Play Pause buttons work correctly
2024-05-22 midi interpreter class (not working)
    [Midi Interpreter class.py, midi_interpreter3.py]
2024-05-24 motor script in right folder + fix for the python class
    [Midi Interpreter class.py, new_motor_script.ino]
2024-05-26 frontend VideoFromCV component add cams selection buttons
2024-05-27 change the progress bar to ServoMotorInstruction component
2024-05-27 buttons API calls VideoFromCV component
2024-05-27 two buttons with API calls done
2024-05-28 ServoMotorInstruction component API calls established
2024-05-28 fetch fileList in Dashboard then pass it down to the ServoMotorInstruction
2024-05-30 midi plays successfully, file library contains one playable file, still read to fix
    [actions.py, core.py, midi_recorder.py]
2024-05-30 try to fix from here
    [api.py]
2024-05-30 one problem solved : the backend api and the websocket having the same port number
    [api.py, main.py]
2024-05-30 electronic schematics
    [electronic sketch 1.fzz, electronic sketch 2.fzz]
2024-05-30 project files in stl, step, f3d/f3z and dxf
    [adjustable_finger_wrap.f3d, adjustable_finger_wrap.step, adjustable_finger_wraps.stl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]
2024-05-30 new photo added
    [pyvenv.cfg]
